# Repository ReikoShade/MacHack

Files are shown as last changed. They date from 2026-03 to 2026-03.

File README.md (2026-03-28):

# MacHack v0.1

MacHack is a mini hydroponic system designed to fit inside an old Apple Mac Pro case. Powered by a Raspberry Pi Pico and MiniFermer light.

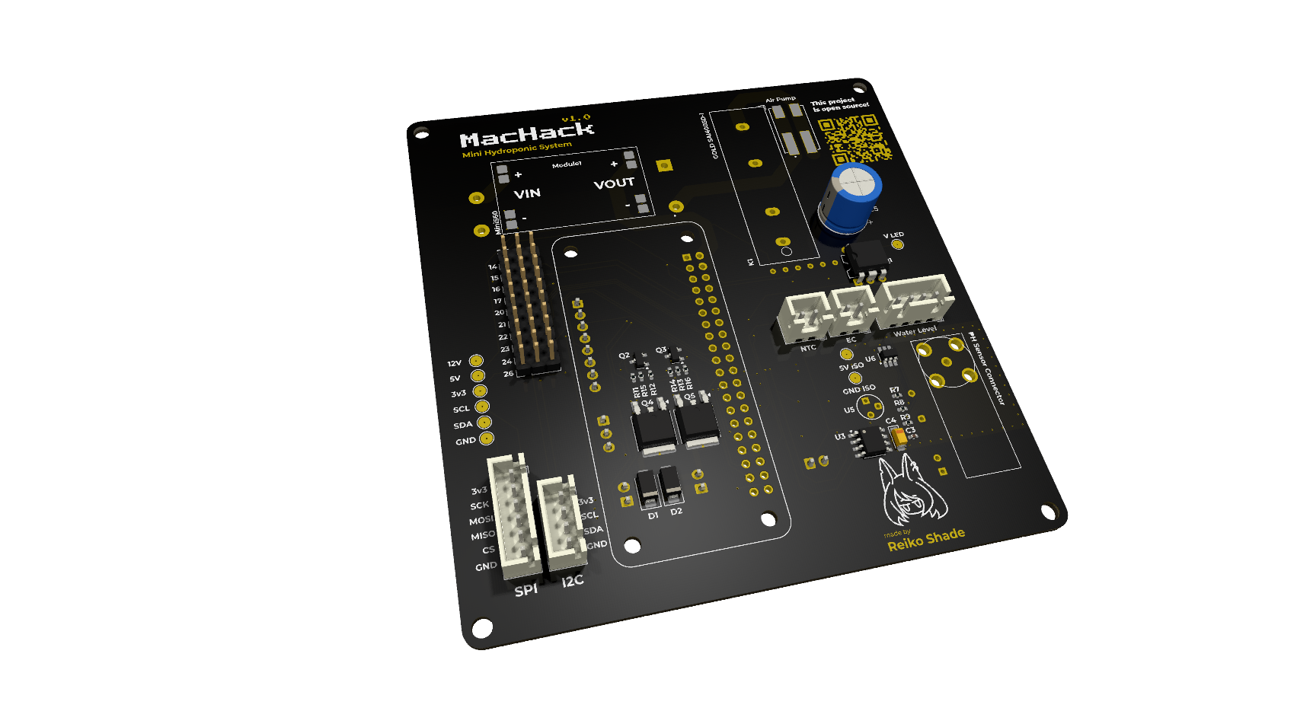
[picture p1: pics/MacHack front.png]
MacHack front


### Features
#### Control:
- Light
- Solution pump
- Air pump
- Fan

#### Monitoring:
- Light level
- Air temperature
- Humidity
- Nutrient solution level
- EC/Root temperature
- pH Level

#### User Interaction
- Display
- Button
- Web Interface

## Main Components BOM

- Apple Mac Pro 2009 case (or any other metal PC case)
- Raspberry Pi Pico
- MiniFermer Quantum board 180x390mm
- Small Circle SPI Display (240x240 GC9A01 or similar)

## PCB BOM
|Идентиф.|Обозначение |Посад. место |Количество|Значение |
|---|---|---|---|---|
|1 |J14 |JST_XH_B6B-XH-A_1x06_P2.50mm_Vertical |1 |SPI |
|2 |R7,R8,R9 |R_0402_1005Metric_Pad0.72x0.64mm_HandSolder |3 |4.7K |
|3 |TP9 |TestPoint_Pad_D2.0mm |1 |12V |
|4 |J11 |PinHeader_1x03_P2.54mm_Vertical |1 |Conn_GPIO_20 |
|5 |J26,J23 |WAGO_2060-452_998-404 |2 |ac |
|6 |Q5,Q4 |TO-252-2 |2 |IRLR8726PBF |
|7 |J9 |JST_XH_B2B-XH-A_1x02_P2.50mm_Vertical |1 |EC |
|8 |TP8 |TestPoint_Pad_D2.0mm |1 |V_LED |
|9 |J3 |PinHeader_1x03_P2.54mm_Vertical |1 |Conn_GPIO_21 |
|10 |J5 |JST_XH_B2B-XH-A_1x02_P2.50mm_Vertical |1 |NTC |
|11 |D2,D1 |D_SMA |2 |SS34 |
|12 |C3 |C_0402_1005Metric_Pad0.74x0.62mm_HandSolder |1 |0.1uF |
|13 |J25 |PinHeader_1x03_P2.54mm_Vertical |1 |Conn_GPIO_26 |
|14 |R14,R12,R11,R13,R3|R_0402_1005Metric_Pad0.72x0.64mm_HandSolder |5 |10k |
|15 |TP3 |TestPoint_Pad_D2.0mm |1 |SCL |
|16 |J24 |JST_XH_B4B-XH-A_1x04_P2.50mm_Vertical |1 |Water Level Sensor |
|17 |Q2,Q3 |SOT-23 |2 |BSS138 |
|18 |R16,R15,R1 |R_0402_1005Metric_Pad0.72x0.64mm_HandSolder |3 |510 |
|19 |U6 |SOT-23-6_Handsoldering |1 |MCP3421A0T-E_CH |
|20 |J12 |PinHeader_1x03_P2.54mm_Vertical |1 |Conn_GPIO_23 |
|21 |C5 |CP_Radial_D10.0mm_P3.80mm |1 |C_Polarized |
|22 |TP7 |TestPoint_Pad_D2.0mm |1 |GND_PH |
|23 |U3 |SOIC-8_3.9x4.9mm_P1.27mm |1 |ISO1540 |
|24 |Module1 |Mini560 |1 |~ |
|25 |TP2 |TestPoint_Pad_D2.0mm |1 |3.3V |
|26 |TP6 |TestPoint_Pad_D2.0mm |1 |5V_PH |
|27 |J7 |PinHeader_1x03_P2.54mm_Vertical |1 |Conn_GPIO_17 |
|28 |J6 |PinHeader_1x03_P2.54mm_Vertical |1 |Conn_GPIO_14 |
|29 |J16 |DOSIN-801-0051-thumbnail1DOSIN-801-0051 |1 |PH Sensor |
|30 |J13 |PinHeader_1x03_P2.54mm_Vertical |1 |Conn_GPIO_24 |
|31 |Q1 |DIP-6_W7.62mm |1 |~ |
|32 |K1 |GOLD DDR SAI4005D_I |1 |Relay_SPST-NC |
|33 |C4 |CP_EIA-3216-18_Kemet-A_Pad1.58x1.35mm_HandSolder |1 |10uF |
|34 |J15 |JST_XH_B4B-XH-A_1x04_P2.50mm_Vertical |1 |I2C |
|35 |J10 |PinHeader_1x03_P2.54mm_Vertical |1 |Conn_GPIO_15 |
|36 |U5 |LM336Z25 |1 |LM336Z25 |
|37 |J2 |PinHeader_1x03_P2.54mm_Vertical |1 |Conn_GPIO_16 |
|38 |U1 |MODULE_RASPBERRY_PI_ZERO_2_W |1 |RASPBERRY_PI_ZERO_2_W|
|39 |TP5 |TestPoint_Pad_D2.0mm |1 |GND |
|40 |TP1 |TestPoint_Pad_D2.0mm |1 |5V |
|41 |TP4 |TestPoint_Pad_D2.0mm |1 |SDA |
|42 |J8 |PinHeader_1x03_P2.54mm_Vertical |1 |Conn_GPIO_22 |
|43 |R10 |SolderJumper-2_P1.3mm_Bridged_RoundedPad1.0x1.5mm|1 |0 |
|44 |PS1 |B1205S-2WR2 |1 |B1205S-2WR2 |
|45 |J22 |WAGO_2060-452_998-404 |1 |driver |
|46 |U7 |SOIC-8_3.9x4.9mm_P1.27mm |1 |MCP602-I_P |
|47 |J4 |JST_XH_B2B-XH-A_1x02_P2.50mm_Vertical |1 |Photo Resistor |
|48 |J18 |JST_XH_B3B-XH-A_1x03_P2.50mm_Vertical |1 |Sensor Button |
|49 |J21 |JST_XH_B2B-XH-A_1x02_P2.50mm_Vertical |1 |Fan |
|50 |J19 |WAGO_2060-452_998-404 |1 |minifermer |
|51 |JP1 |SolderJumper-2_P1.3mm_Open_RoundedPad1.0x1.5mm |1 |Water Level Mode |
|52 |R2 |R_0402_1005Metric_Pad0.72x0.64mm_HandSolder |1 |100K |
|53 |U2 |HW-611 |1 |HW-611 |
|54 |R5,R4 |R_0402_1005Metric_Pad0.72x0.64mm_HandSolder |2 |4.7k |
|55 |J17 |JST_XH_B8B-XH-A_1x08_P2.50mm_Vertical |1 |Round_Display |
|56 |U4 |SOIC-16_3.9x9.9mm_P1.27mm |1 |MCP3008 |
|57 |J20 |JST_XH_B2B-XH-A_1x02_P2.50mm_Vertical |1 |Pump |
|58 |C2,C1 |C_0402_1005Metric_Pad0.74x0.62mm_HandSolder |2 |100nF |
|59 |PS2 |Converter_ACDC_MeanWell_IRM-10-xx_THT |1 |IRM-10-12 |

## Project Stage
### PCB and Components

PCB v1.0 designed and manufactured. Errors were found in the footprints of components HW-611 and B1205S-2WR2 and temporarily fixed with some "creative" soldering, brute force and magic.

Soldering in progress... Still waiting for some components to arrive for a full board test.

But it’s alive! Outputs 12V, 5V and no short circuits somehow.

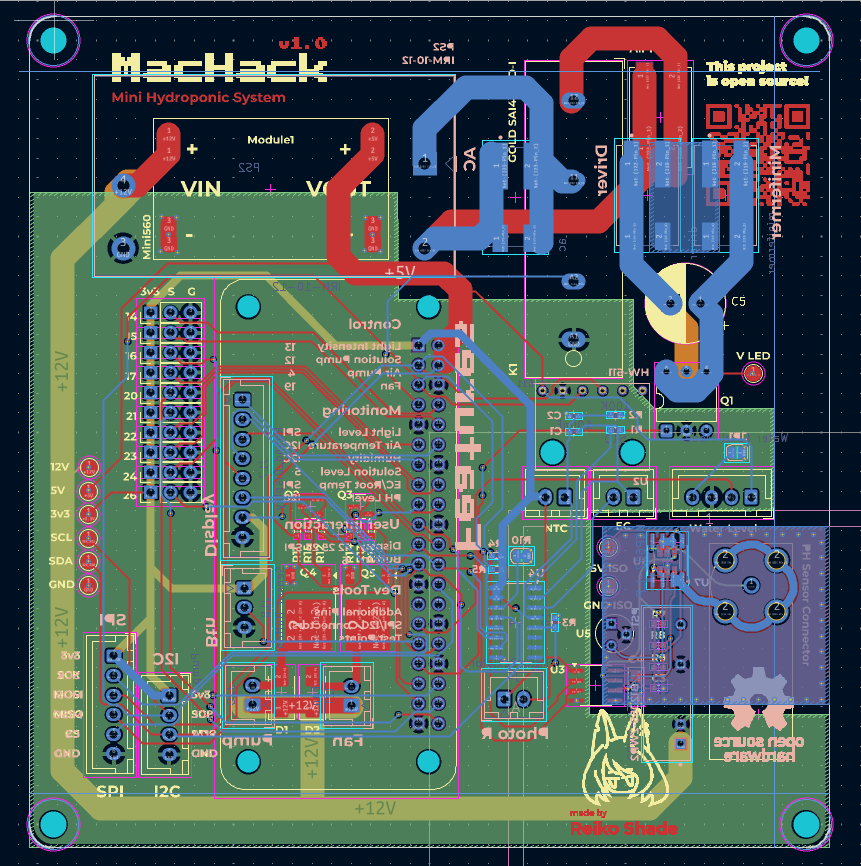
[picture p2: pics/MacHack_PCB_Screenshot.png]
MacHack PCB desigh

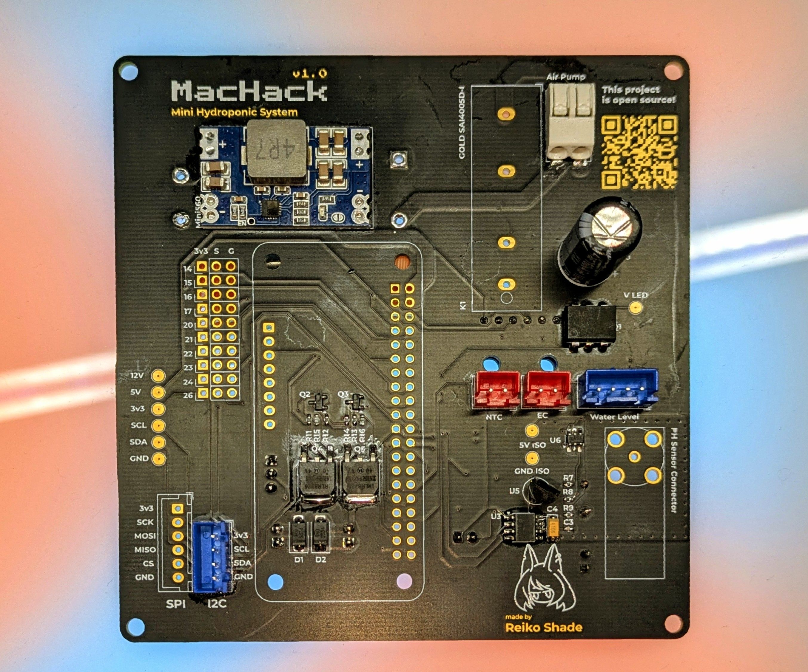
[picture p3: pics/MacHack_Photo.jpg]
MacHack soldering in progress


### Code

Code is on hold until the device is fully assembled and running.

## Thanks!

This is my first PCB and my first step into circuit engineering. It was manufactured with the help of School21’s Lab. A huge shout-out to them for the equipment, training and assistance throughout the process!

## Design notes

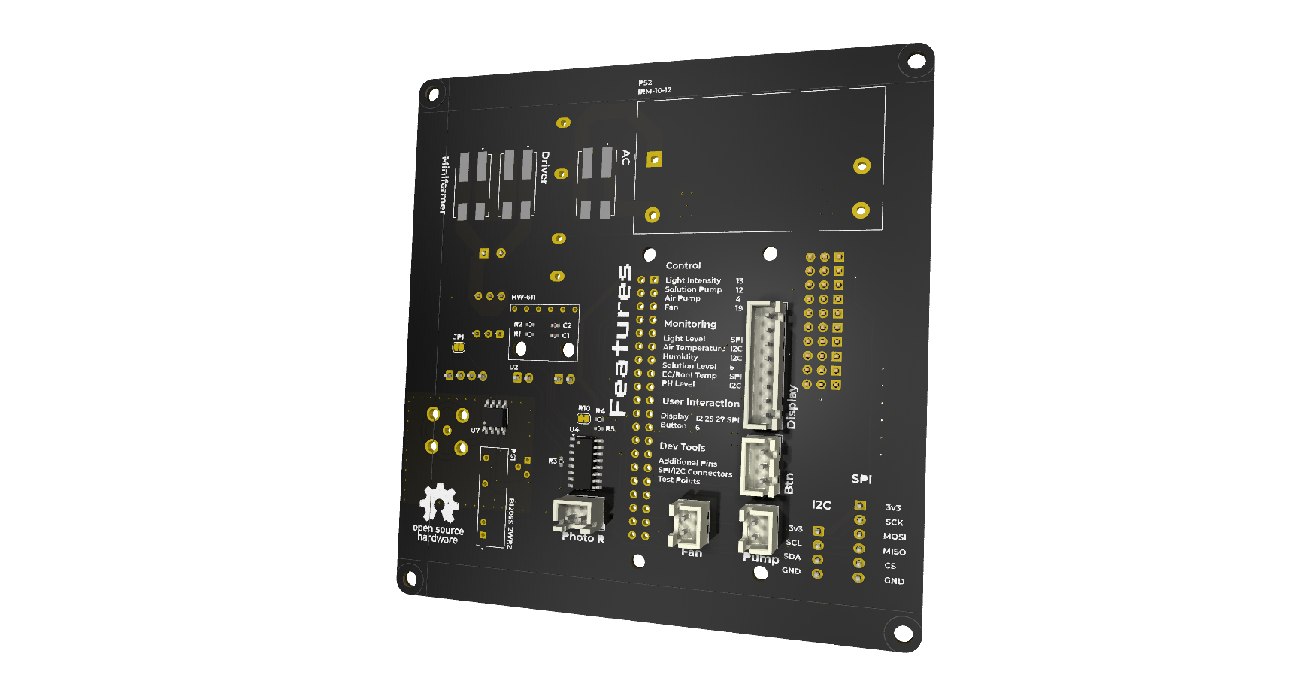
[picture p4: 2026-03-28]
pics/MacHack back.png

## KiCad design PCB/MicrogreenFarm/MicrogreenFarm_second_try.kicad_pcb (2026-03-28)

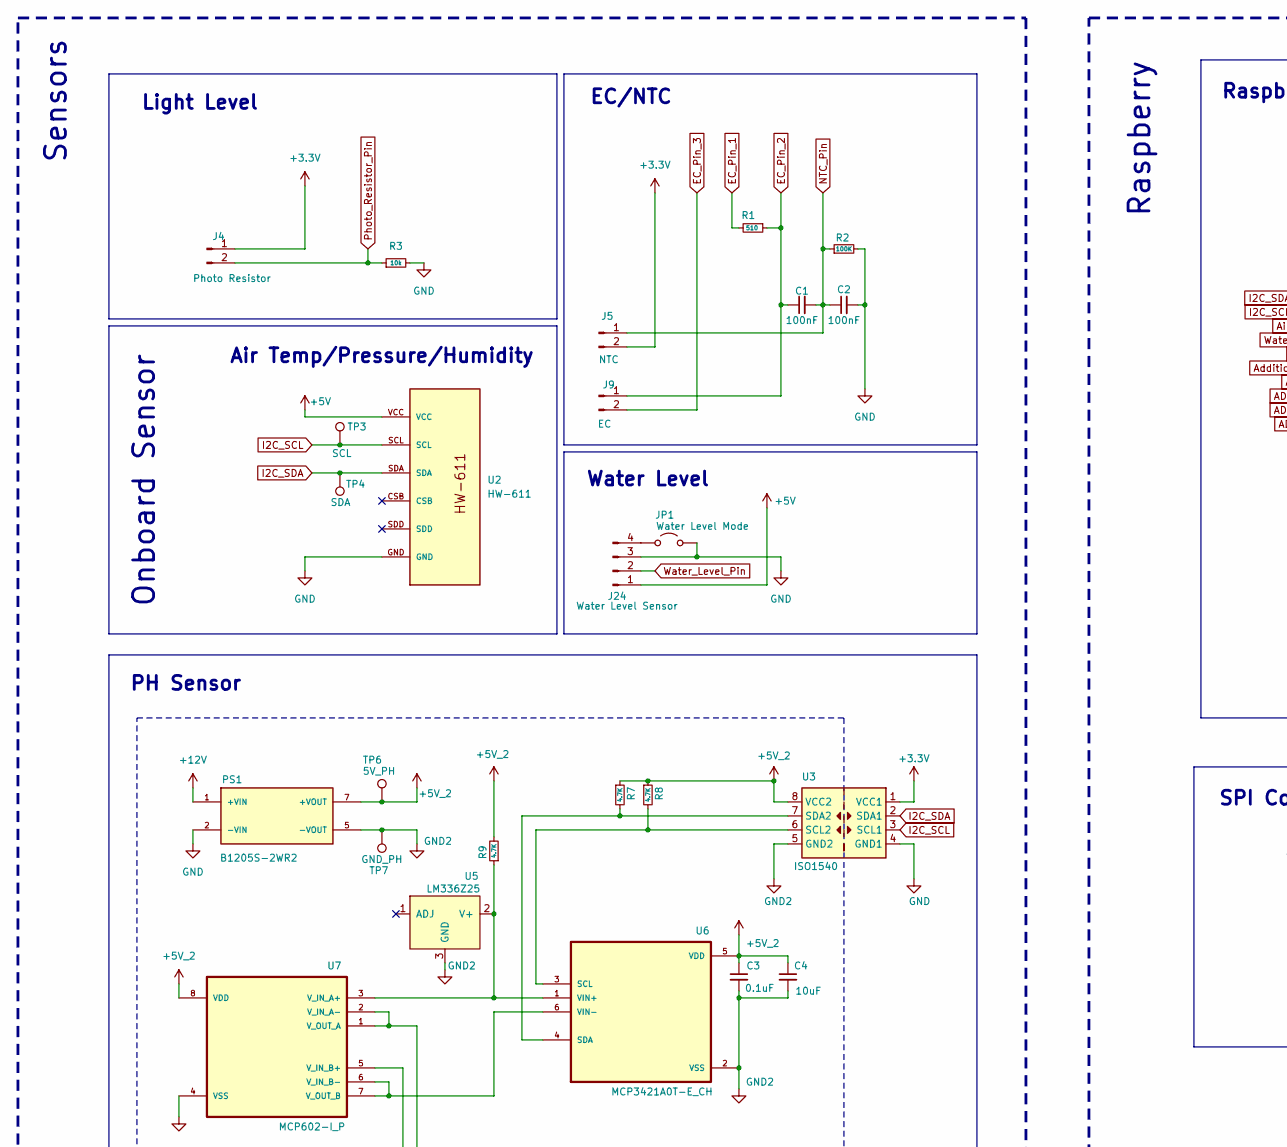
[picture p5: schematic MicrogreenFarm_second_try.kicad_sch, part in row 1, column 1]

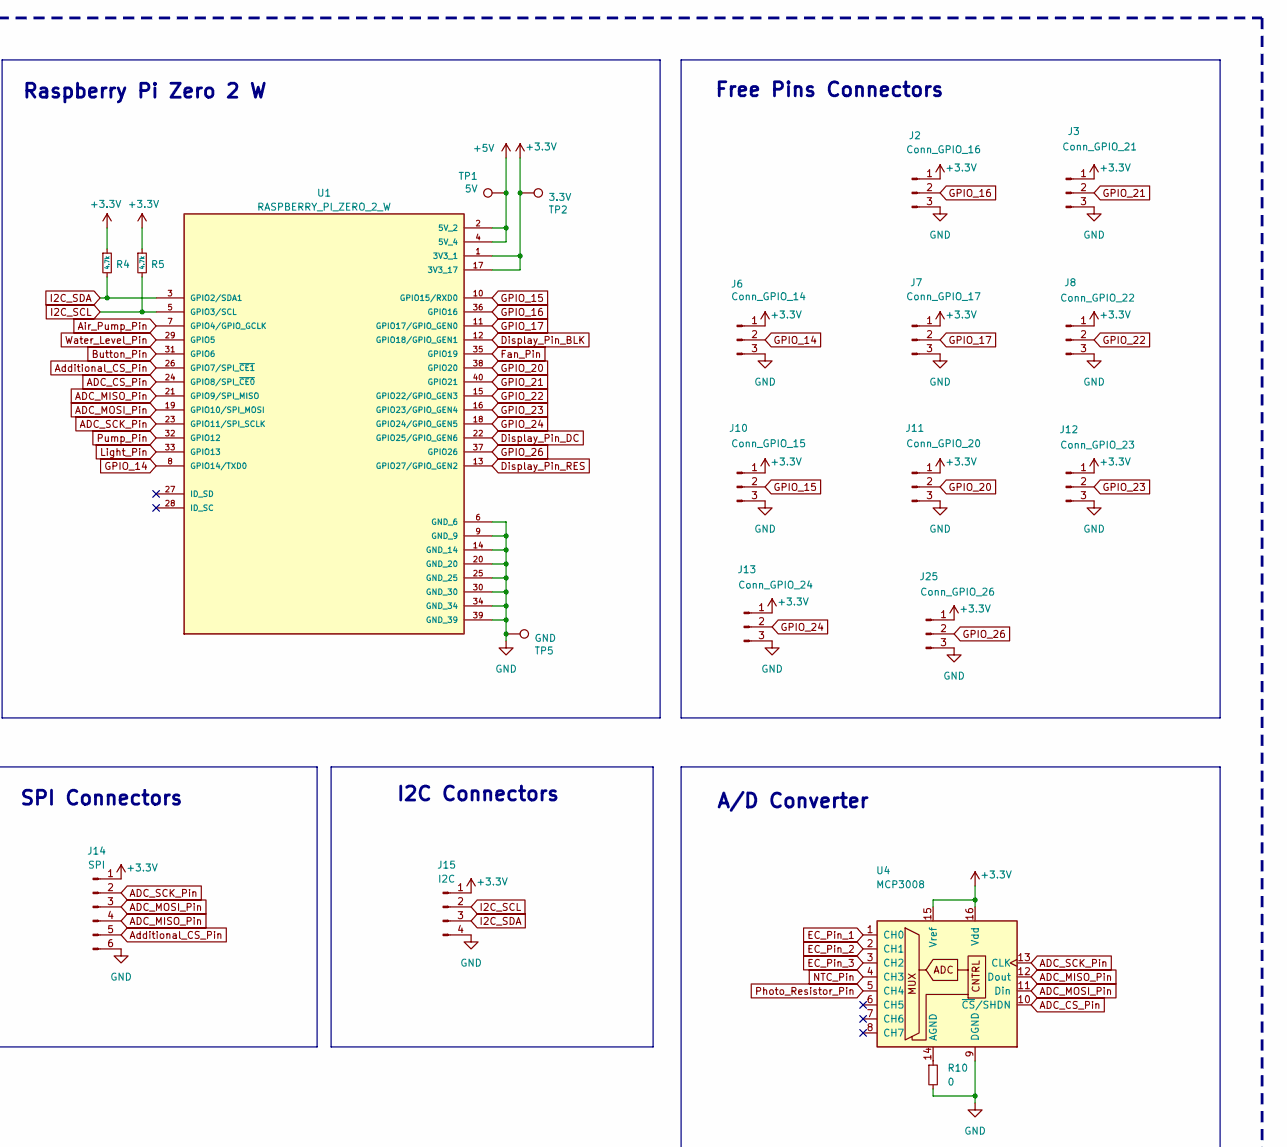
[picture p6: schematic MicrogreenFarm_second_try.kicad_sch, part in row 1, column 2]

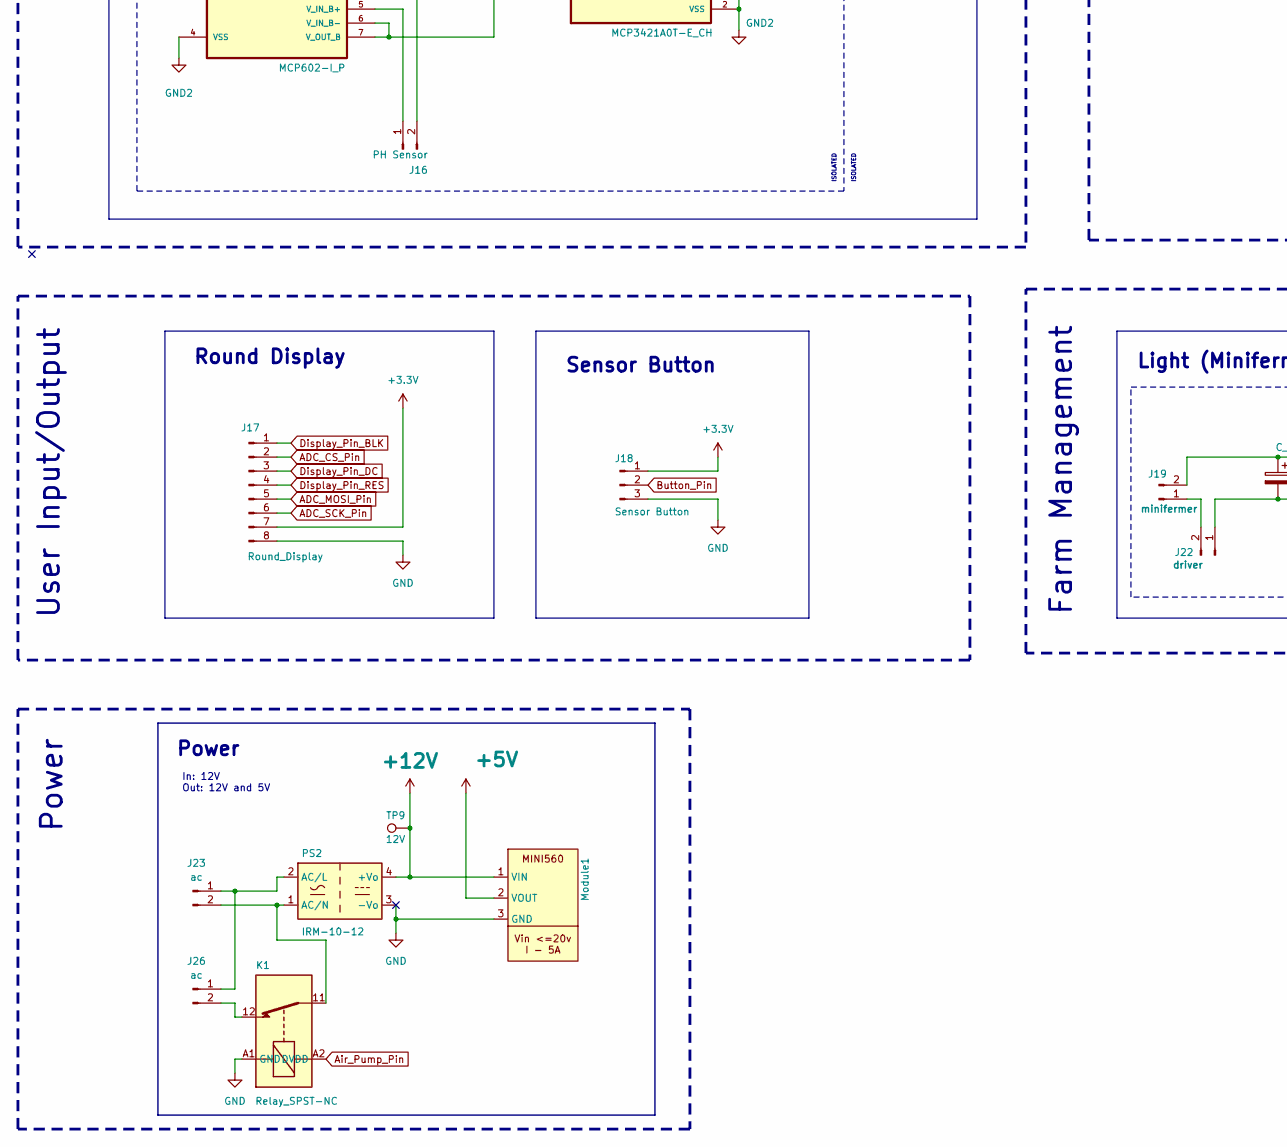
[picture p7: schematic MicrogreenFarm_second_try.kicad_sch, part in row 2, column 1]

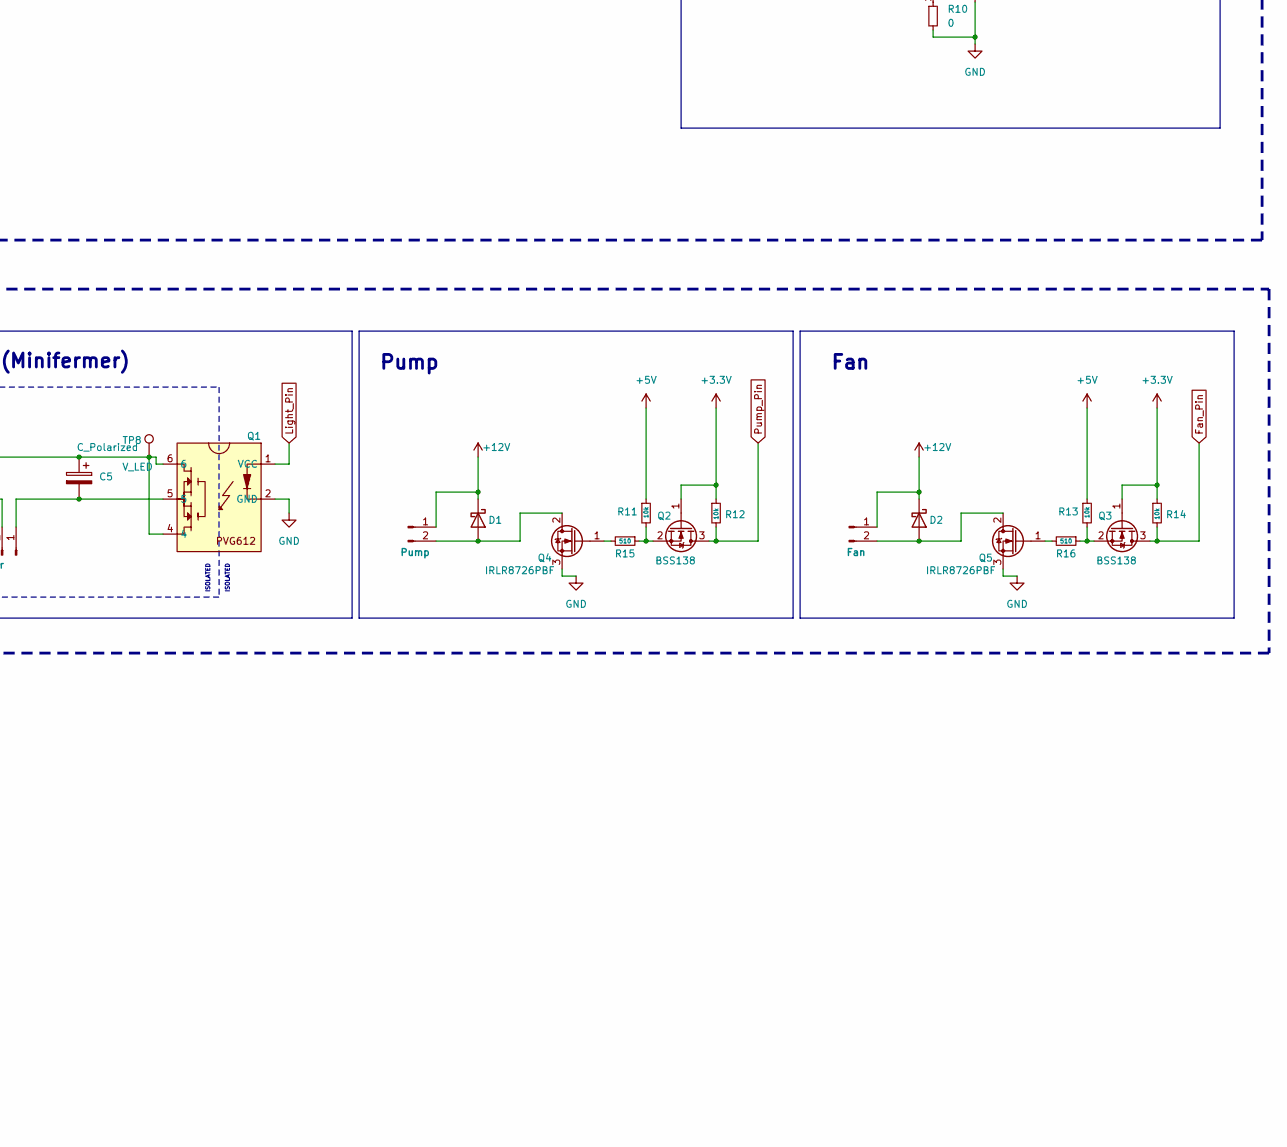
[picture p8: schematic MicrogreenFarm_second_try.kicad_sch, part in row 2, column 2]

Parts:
C1, C2: 100nF; C_0402_1005Metric_Pad0.74x0.62mm_HandSolder
C3: 0.1uF; C_0402_1005Metric_Pad0.74x0.62mm_HandSolder
C4: 10uF; CP_EIA-3216-18_Kemet-A_Pad1.58x1.35mm_HandSolder
C5: C_Polarized; CP_Radial_D10.0mm_P3.80mm
D1, D2: SS34; D_SMA
J2: Conn_GPIO_16; PinHeader_1x03_P2.54mm_Vertical
J3: Conn_GPIO_21; PinHeader_1x03_P2.54mm_Vertical
J4: Photo Resistor; JST_XH_B2B-XH-A_1x02_P2.50mm_Vertical
J5: NTC; JST_XH_B2B-XH-A_1x02_P2.50mm_Vertical
J6: Conn_GPIO_14; PinHeader_1x03_P2.54mm_Vertical
J7: Conn_GPIO_17; PinHeader_1x03_P2.54mm_Vertical
J8: Conn_GPIO_22; PinHeader_1x03_P2.54mm_Vertical
J9: EC; JST_XH_B2B-XH-A_1x02_P2.50mm_Vertical
J10: Conn_GPIO_15; PinHeader_1x03_P2.54mm_Vertical
J11: Conn_GPIO_20; PinHeader_1x03_P2.54mm_Vertical
J12: Conn_GPIO_23; PinHeader_1x03_P2.54mm_Vertical
J13: Conn_GPIO_24; PinHeader_1x03_P2.54mm_Vertical
J14: SPI; JST_XH_B6B-XH-A_1x06_P2.50mm_Vertical
J15: I2C; JST_XH_B4B-XH-A_1x04_P2.50mm_Vertical
J16: PH Sensor; DOSIN-801-0051-thumbnail1DOSIN-801-0051
J17: Round_Display; JST_XH_B8B-XH-A_1x08_P2.50mm_Vertical
J18: Sensor Button; JST_XH_B3B-XH-A_1x03_P2.50mm_Vertical
J19: minifermer; WAGO_2060-452_998-404
J20: Pump; JST_XH_B2B-XH-A_1x02_P2.50mm_Vertical
J21: Fan; JST_XH_B2B-XH-A_1x02_P2.50mm_Vertical
J22: driver; WAGO_2060-452_998-404
J23, J26: ac; WAGO_2060-452_998-404
J24: Water Level Sensor; JST_XH_B4B-XH-A_1x04_P2.50mm_Vertical
J25: Conn_GPIO_26; PinHeader_1x03_P2.54mm_Vertical
JP1: Water Level Mode; SolderJumper-2_P1.3mm_Open_RoundedPad1.0x1.5mm
K1: Relay_SPST-NC; GOLD DDR SAI4005D_I
Module1: Mini560
PS1: B1205S-2WR2; PARTREV 2023-1.2
PS2: IRM-10-12; Converter_ACDC_MeanWell_IRM-10-xx_THT
Q1: DIP-6_W7.62mm
Q2, Q3: BSS138; SOT-23
Q4, Q5: IRLR8726PBF; TO-252-2
R1, R15, R16: 510; R_0402_1005Metric_Pad0.72x0.64mm_HandSolder
R2: 100K; R_0402_1005Metric_Pad0.72x0.64mm_HandSolder
R3, R11, R12, R13, R14: 10k; R_0402_1005Metric_Pad0.72x0.64mm_HandSolder
R4, R5: 4.7k; R_0402_1005Metric_Pad0.72x0.64mm_HandSolder
R7, R8, R9: 4.7K; R_0402_1005Metric_Pad0.72x0.64mm_HandSolder
R10: 0; SolderJumper-2_P1.3mm_Bridged_RoundedPad1.0x1.5mm
TP1: 5V; TestPoint_Pad_D2.0mm
TP2: 3.3V; TestPoint_Pad_D2.0mm
TP3: SCL; TestPoint_Pad_D2.0mm
TP4: SDA; TestPoint_Pad_D2.0mm
TP5: GND; TestPoint_Pad_D2.0mm
TP6: 5V_PH; TestPoint_Pad_D2.0mm
TP7: GND_PH; TestPoint_Pad_D2.0mm
TP8: V_LED; TestPoint_Pad_D2.0mm
TP9: 12V; TestPoint_Pad_D2.0mm
U1: RASPBERRY_PI_ZERO_2_W; MODULE_RASPBERRY_PI_ZERO_2_W; PARTREV April 2024
U2: HW-611
U3: ISO1540; SOIC-8_3.9x4.9mm_P1.27mm
U4: MCP3008; SOIC-16_3.9x9.9mm_P1.27mm
U5: LM336Z25
U6: MCP3421A0T-E_CH; SOT-23-6_Handsoldering
U7: MCP602-I_P; SOIC-8_3.9x4.9mm_P1.27mm

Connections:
+3.3V: J2.1, J3.1, J4.1, J5.2, J6.1, J7.1, J8.1, J10.1, J11.1, J12.1, J13.1, J14.1, J15.1, J17.7, J18.1, J25.1, Q2.1 (G), Q3.1 (G), R4.1, R5.1, R12.1, R14.1, TP2.1, U1.1 (3V3_1), U1.17 (3V3_17), U3.1 (VCC1), U4.15 (Vref), U4.16 (Vdd)
+5V: J24.1, Module1.2 (VOUT), R11.1, R13.1, TP1.1, U1.2 (5V_2), U1.4 (5V_4), U2.VCC
+5V_2: C3.1, C4.1, PS1.7 (+VOUT), R7.1, R8.1, R9.2, TP6.1, U3.8 (VCC2), U6.5 (VDD), U7.8 (VDD)
+12V: D1.1 (K), D2.1 (K), J20.1, J21.1, Module1.1 (VIN), PS1.1 (+VIN), PS2.4 (+Vo), TP9.1
ADC_CS_Pin: J17.2, U1.24 (GPIO8/SPI_~CE0), U4.10 (~CS/SHDN)
ADC_MISO_Pin: J14.4, U1.21 (GPIO9/SPI_MISO), U4.12 (Dout)
ADC_MOSI_Pin: J14.3, J17.5, U1.19 (GPIO10/SPI_MOSI), U4.11 (Din)
ADC_SCK_Pin: J14.2, J17.6, U1.23 (GPIO11/SPI_SCLK), U4.13 (CLK)
Additional_CS_Pin: J14.5, U1.26 (GPIO7/SPI_~CE1)
Air_Pump_Pin: K1.A2 (DVDD), U1.7 (GPIO4/GPIO_GCLK)
Button_Pin: J18.2, U1.31 (GPIO6)
Display_Pin_BLK: J17.1, U1.12 (GPIO18/GPIO_GEN1)
Display_Pin_DC: J17.3, U1.22 (GPIO25/GPIO_GEN6)
Display_Pin_RES: J17.4, U1.13 (GPIO27/GPIO_GEN2)
EC_Pin_1: R1.2, U4.1 (CH0)
EC_Pin_2: C1.1, J9.1, R1.1, U4.2 (CH1)
EC_Pin_3: J9.2, U4.3 (CH2)
Fan_Pin: Q3.3 (D), R14.2, U1.35 (GPIO19)
GND: C2.2, J2.3, J3.3, J6.3, J7.3, J8.3, J10.3, J11.3, J12.3, J13.3, J14.6, J15.4, J17.8, J18.3, J24.3, J25.3, JP1.2 (B), K1.A1 (GND), Module1.3 (GND), PS1.2 (-VIN), PS2.3 (-Vo), Q1.2 (GND), Q4.3 (S), Q5.3 (S), R2.2, R3.2, R10.2, TP5.1, U1.6 (GND_6), U1.9 (GND_9), U1.14 (GND_14), U1.20 (GND_20), U1.25 (GND_25), U1.30 (GND_30), U1.34 (GND_34), U1.39 (GND_39), U2.GND, U3.4 (GND1), U4.9 (DGND)
GND2: C3.2, C4.2, PS1.5 (-VOUT), TP7.1, U3.5 (GND2), U5.3 (GND), U6.2 (VSS), U7.4 (VSS)
GPIO_14: J6.2, U1.8 (GPIO14/TXD0)
GPIO_15: J10.2, U1.10 (GPIO15/RXD0)
GPIO_16: J2.2, U1.36 (GPIO16)
GPIO_17: J7.2, U1.11 (GPIO17/GPIO_GEN0)
GPIO_20: J11.2, U1.38 (GPIO20)
GPIO_21: J3.2, U1.40 (GPIO21)
GPIO_22: J8.2, U1.15 (GPIO22/GPIO_GEN3)
GPIO_23: J12.2, U1.16 (GPIO23/GPIO_GEN4)
GPIO_24: J13.2, U1.18 (GPIO24/GPIO_GEN5)
GPIO_26: J25.2, U1.37 (GPIO26)
I2C_SCL: J15.2, R5.2, TP3.1, U1.5 (GPIO3/SCL), U2.SCL, U3.3 (SCL1)
I2C_SDA: J15.3, R4.2, TP4.1, U1.3 (GPIO2/SDA1), U2.SDA, U3.2 (SDA1)
Light_Pin: Q1.1 (VCC), U1.33 (GPIO13)
NTC_Pin: C1.2, C2.1, J5.1, R2.1, U4.4 (CH3)
unnamed: D1.2 (A), J20.2, Q4.2 (D)
unnamed: D2.2 (A), J21.2, Q5.2 (D)
unnamed: J16.1, U7.5 (V_IN_B+)
unnamed: J16.2, U7.1 (V_OUT_A), U7.2 (V_IN_A-)
unnamed: J19.1, J22.2
unnamed: C5.1, J19.2, Q1.4, Q1.6, TP8.1
unnamed: C5.2, J22.1, Q1.5
unnamed: J23.1, J26.1, PS2.2 (AC/L)
unnamed: J23.2, K1.11, PS2.1 (AC/N)
unnamed: J24.4, JP1.1 (A)
unnamed: J26.2, K1.12
unnamed: Q2.2 (S), R11.2, R15.1
unnamed: Q3.2 (S), R13.2, R16.1
unnamed: Q4.1 (G), R15.2
unnamed: Q5.1 (G), R16.2
unnamed: R8.2, U3.6 (SCL2), U6.3 (SCL)
unnamed: R7.2, U3.7 (SDA2), U6.4 (SDA)
unnamed: R10.1, U4.14 (AGND)
unnamed: R9.1, U5.2 (V+), U6.1 (VIN+), U7.3 (V_IN_A+)
unnamed: U6.6 (VIN-), U7.6 (V_IN_B-), U7.7 (V_OUT_B)
Photo_Resistor_Pin: J4.2, R3.1, U4.5 (CH4)
Pump_Pin: Q2.3 (D), R12.2, U1.32 (GPIO12)
Water_Level_Pin: J24.2, U1.29 (GPIO5)

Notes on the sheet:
ISOLATED
Farm Management
EC/NTC
Fan
User Input/Output
Power
Round Display
Sensors
In: 12V Out: 12V and 5V
Water Level
Air Temp/Pressure/Humidity
Raspberry
Onboard Sensor
Light (Minifermer)
I2C Connectors
Light Level
A/D Converter
Sensor Button
Free Pins Connectors
SPI Connectors
Pump
PH Sensor
Raspberry Pi Zero 2 W

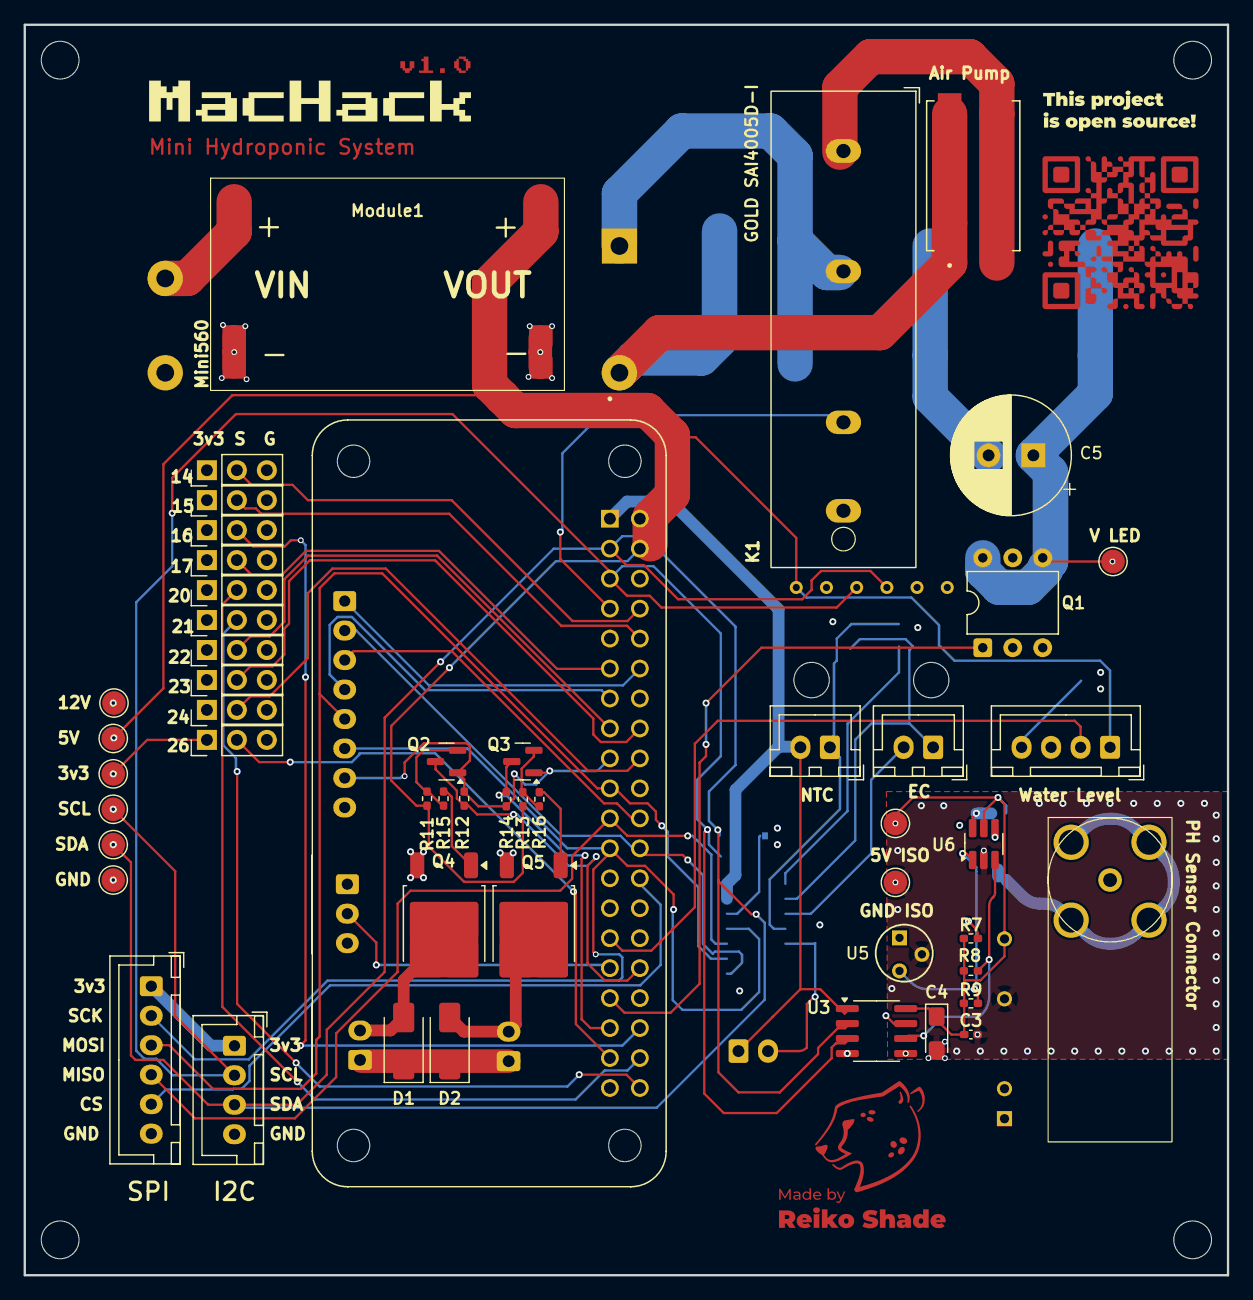
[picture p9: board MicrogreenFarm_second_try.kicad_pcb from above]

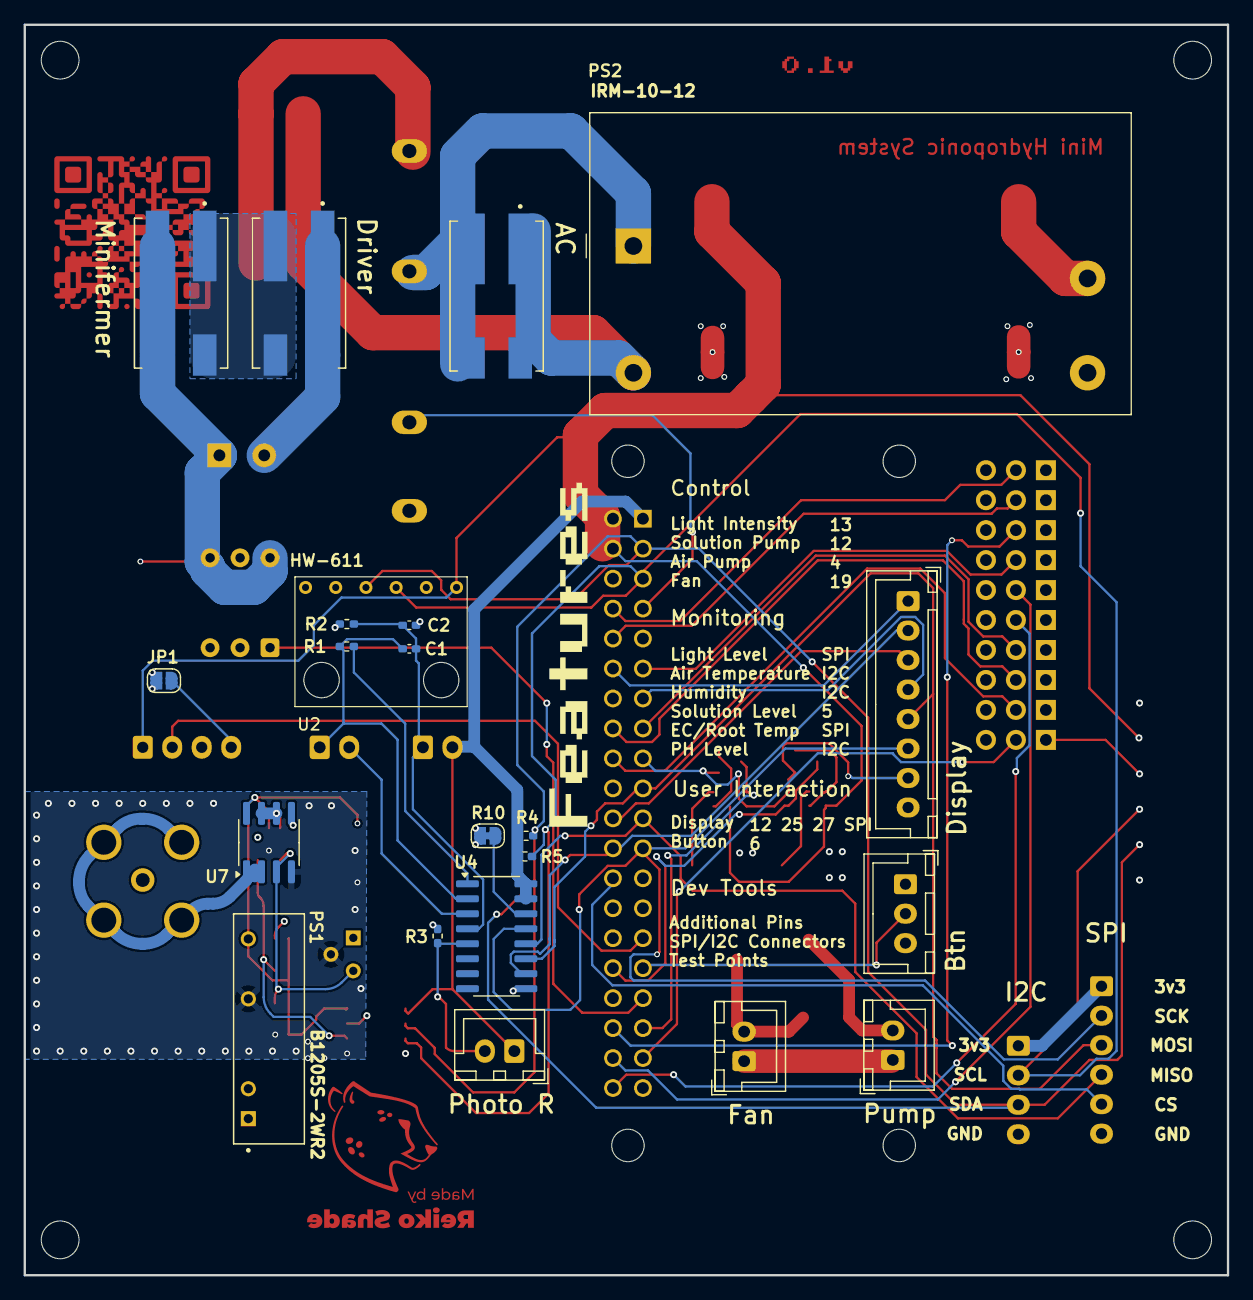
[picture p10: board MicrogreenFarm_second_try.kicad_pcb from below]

Board: 4 copper layers, 102.0 x 106.0 mm, 73 parts (22 on the bottom side), 57 nets.
